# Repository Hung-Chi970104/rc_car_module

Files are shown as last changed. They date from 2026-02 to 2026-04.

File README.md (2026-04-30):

# Rukus: Pocket Robotics Control Computer
Welcome to Rukus! The most powerful and versatile pocket-size robotic control computer that can handle up 18V and 3.2A of peak current. It also features a powerful dual-core RP2040 MCU, allowing users to run heavy computing and even TinyML!

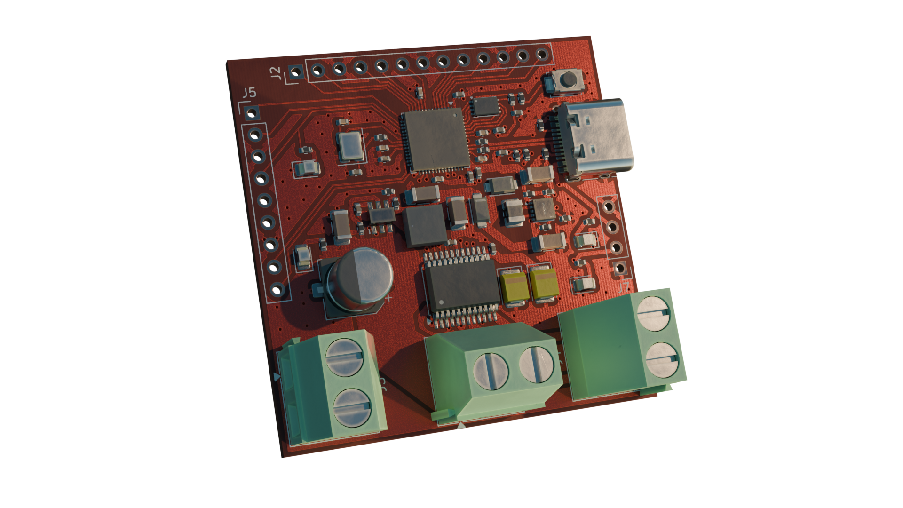
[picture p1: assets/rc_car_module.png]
rendered_image


## Demo Video
https://github.com/user-attachments/assets/a237940f-da78-4733-91b2-979578ba8ca9

https://github.com/user-attachments/assets/f6da3c5c-2f20-4054-9eab-c4b8ad8e2e0a

## Components
- RP2040
- 12MHz Crystal (ABM8-272-T3)
- 4MB Flash Storage (W25Q16JVUXIQ)
- Buck-Boost Switching Regulator 5V to 3V3 (RT6150BGQW)
- Buck-Boost Switching Regulator 12V to 5V (AP64201)
- USB-C (TYPE-C-31-M-12)
- Motor Driver (TB6612FNG)

## PCBs
- 2 layers
- Single-sided component placement
- 2.6mm board thickness
- HASL (with lead) surface finish
- 1oz outer copper weight

### PCB Schematic
schematic

### PCB Layouts
pcb
pcb
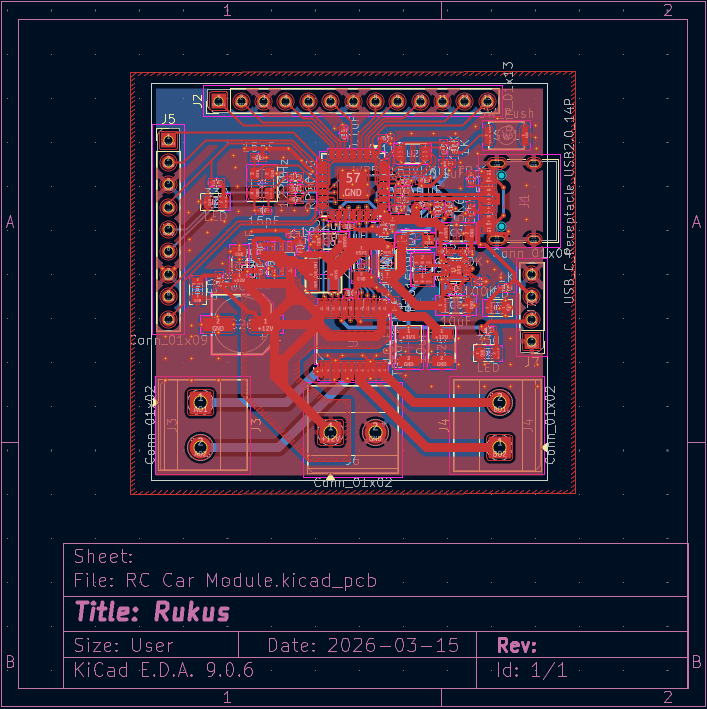
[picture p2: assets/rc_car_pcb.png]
pcb


### 3D Model
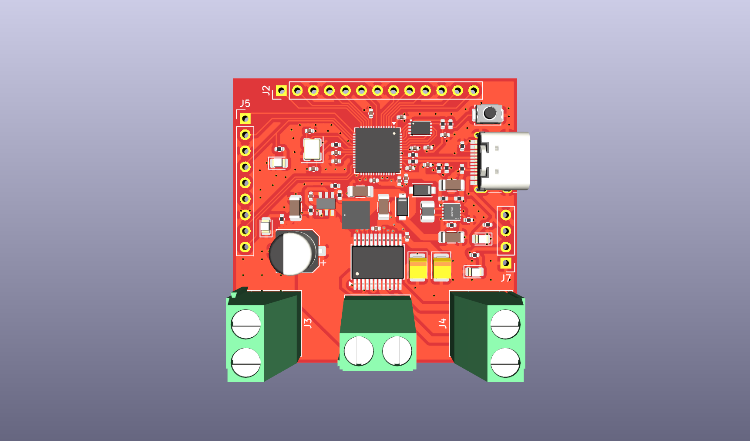
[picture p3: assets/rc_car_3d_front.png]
3d_front

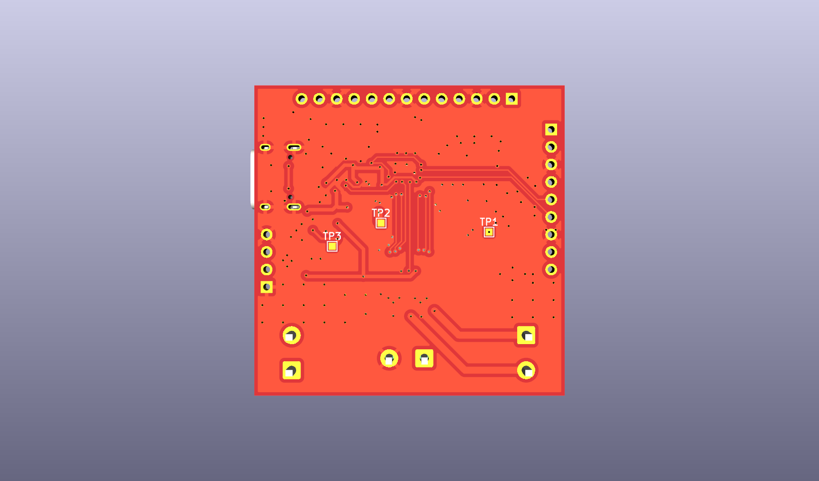
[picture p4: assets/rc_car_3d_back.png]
3d_back


# How to order
- Download the zip file
- Upload the zip file to JLCPCB
- Select PCBA and continue
- Upload BOM.csv and position.csv
- Select the parts and submit payment

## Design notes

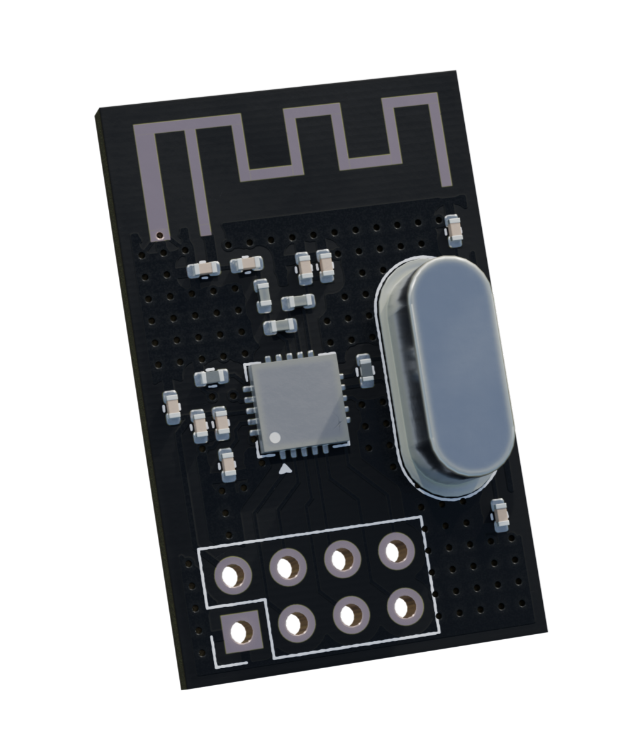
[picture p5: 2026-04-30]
radio/radio.png

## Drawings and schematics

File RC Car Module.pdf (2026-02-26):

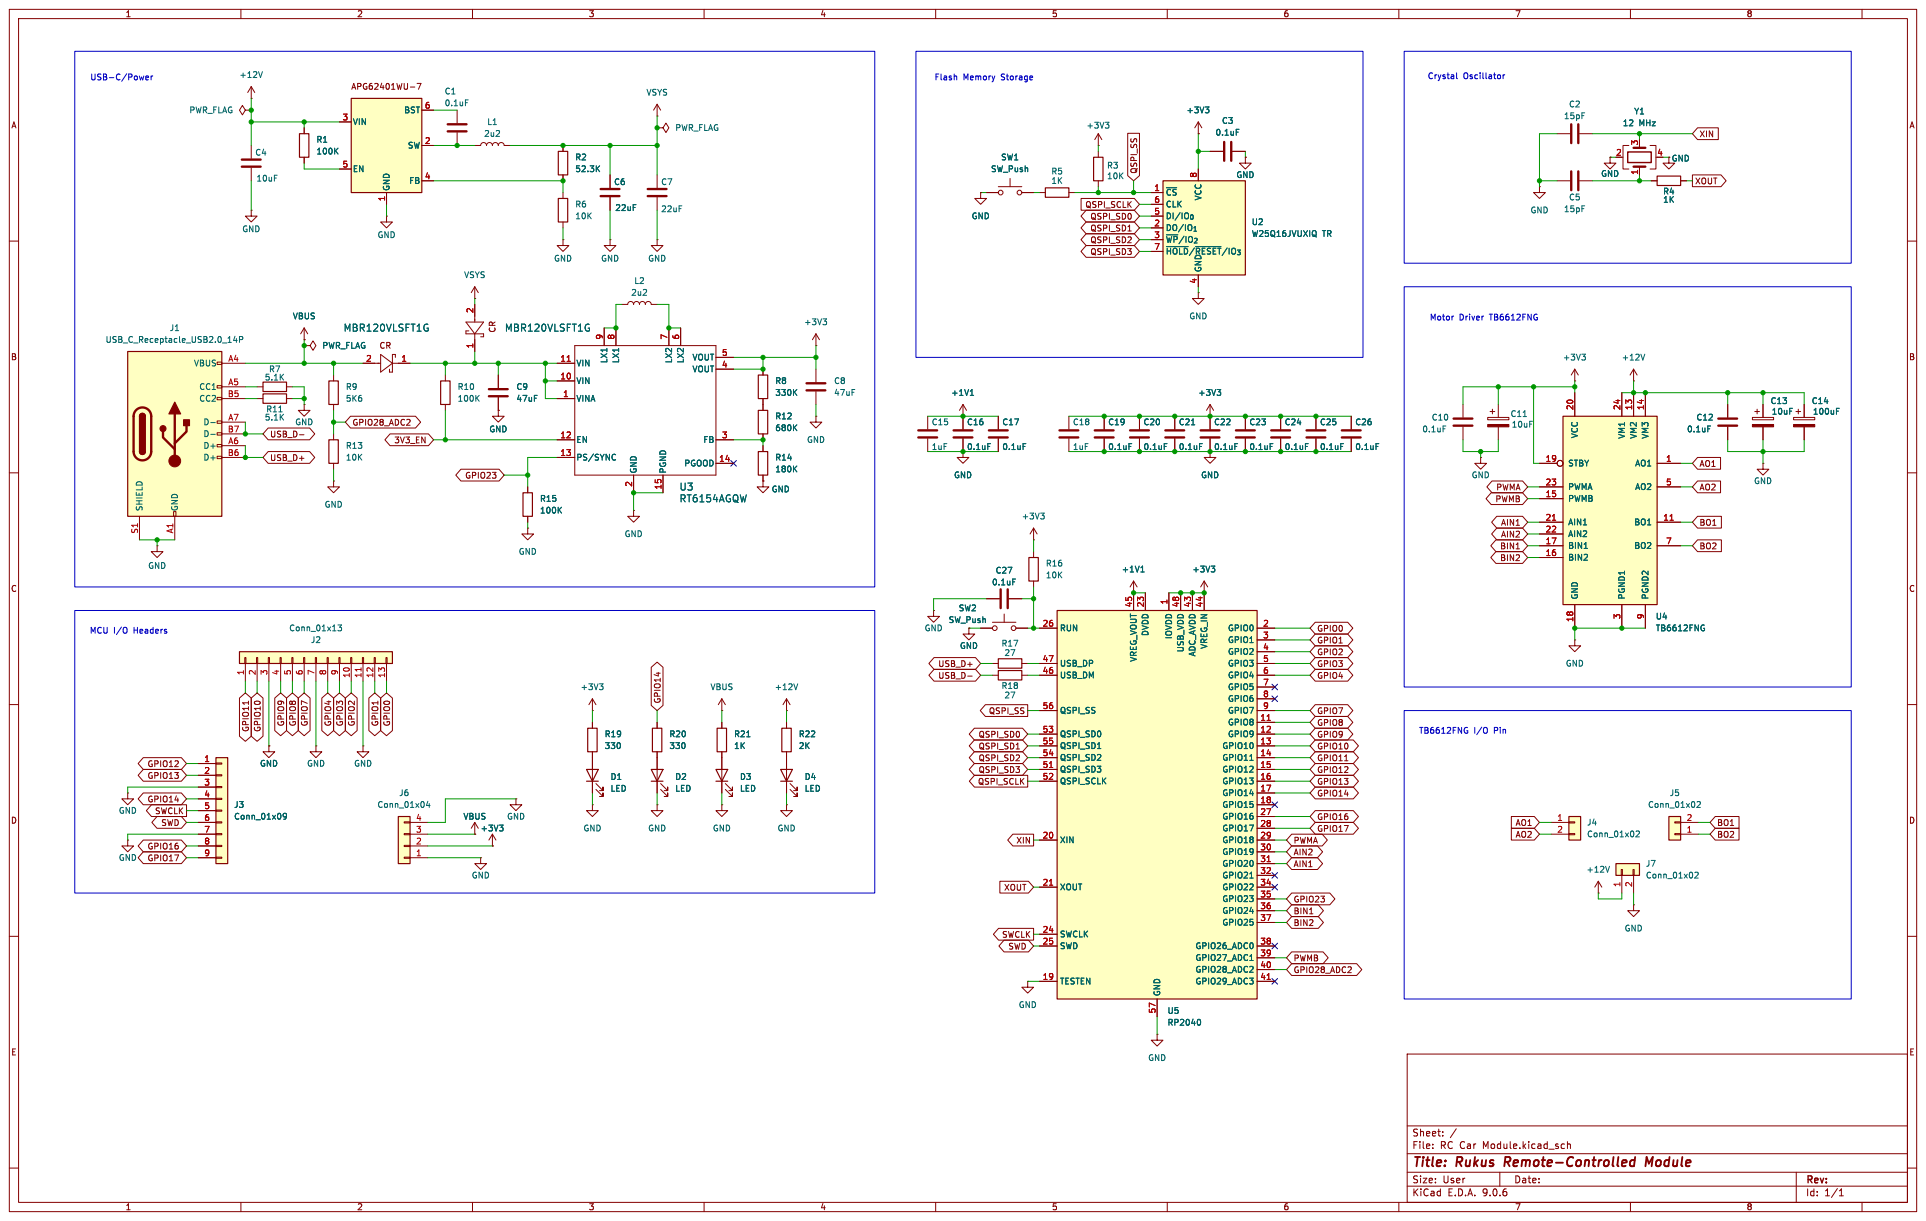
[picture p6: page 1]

1 BST 6 SW 2 FB 4 C1 VSYS

1 BST 6 SW 2 FB 4 GND

6 VOUT 5 VOUT 4 FB 3 PGOOD 14 C9

6 VOUT 5 VOUT 4 FB 3 PGOOD 14 U3 RT6154AGQW

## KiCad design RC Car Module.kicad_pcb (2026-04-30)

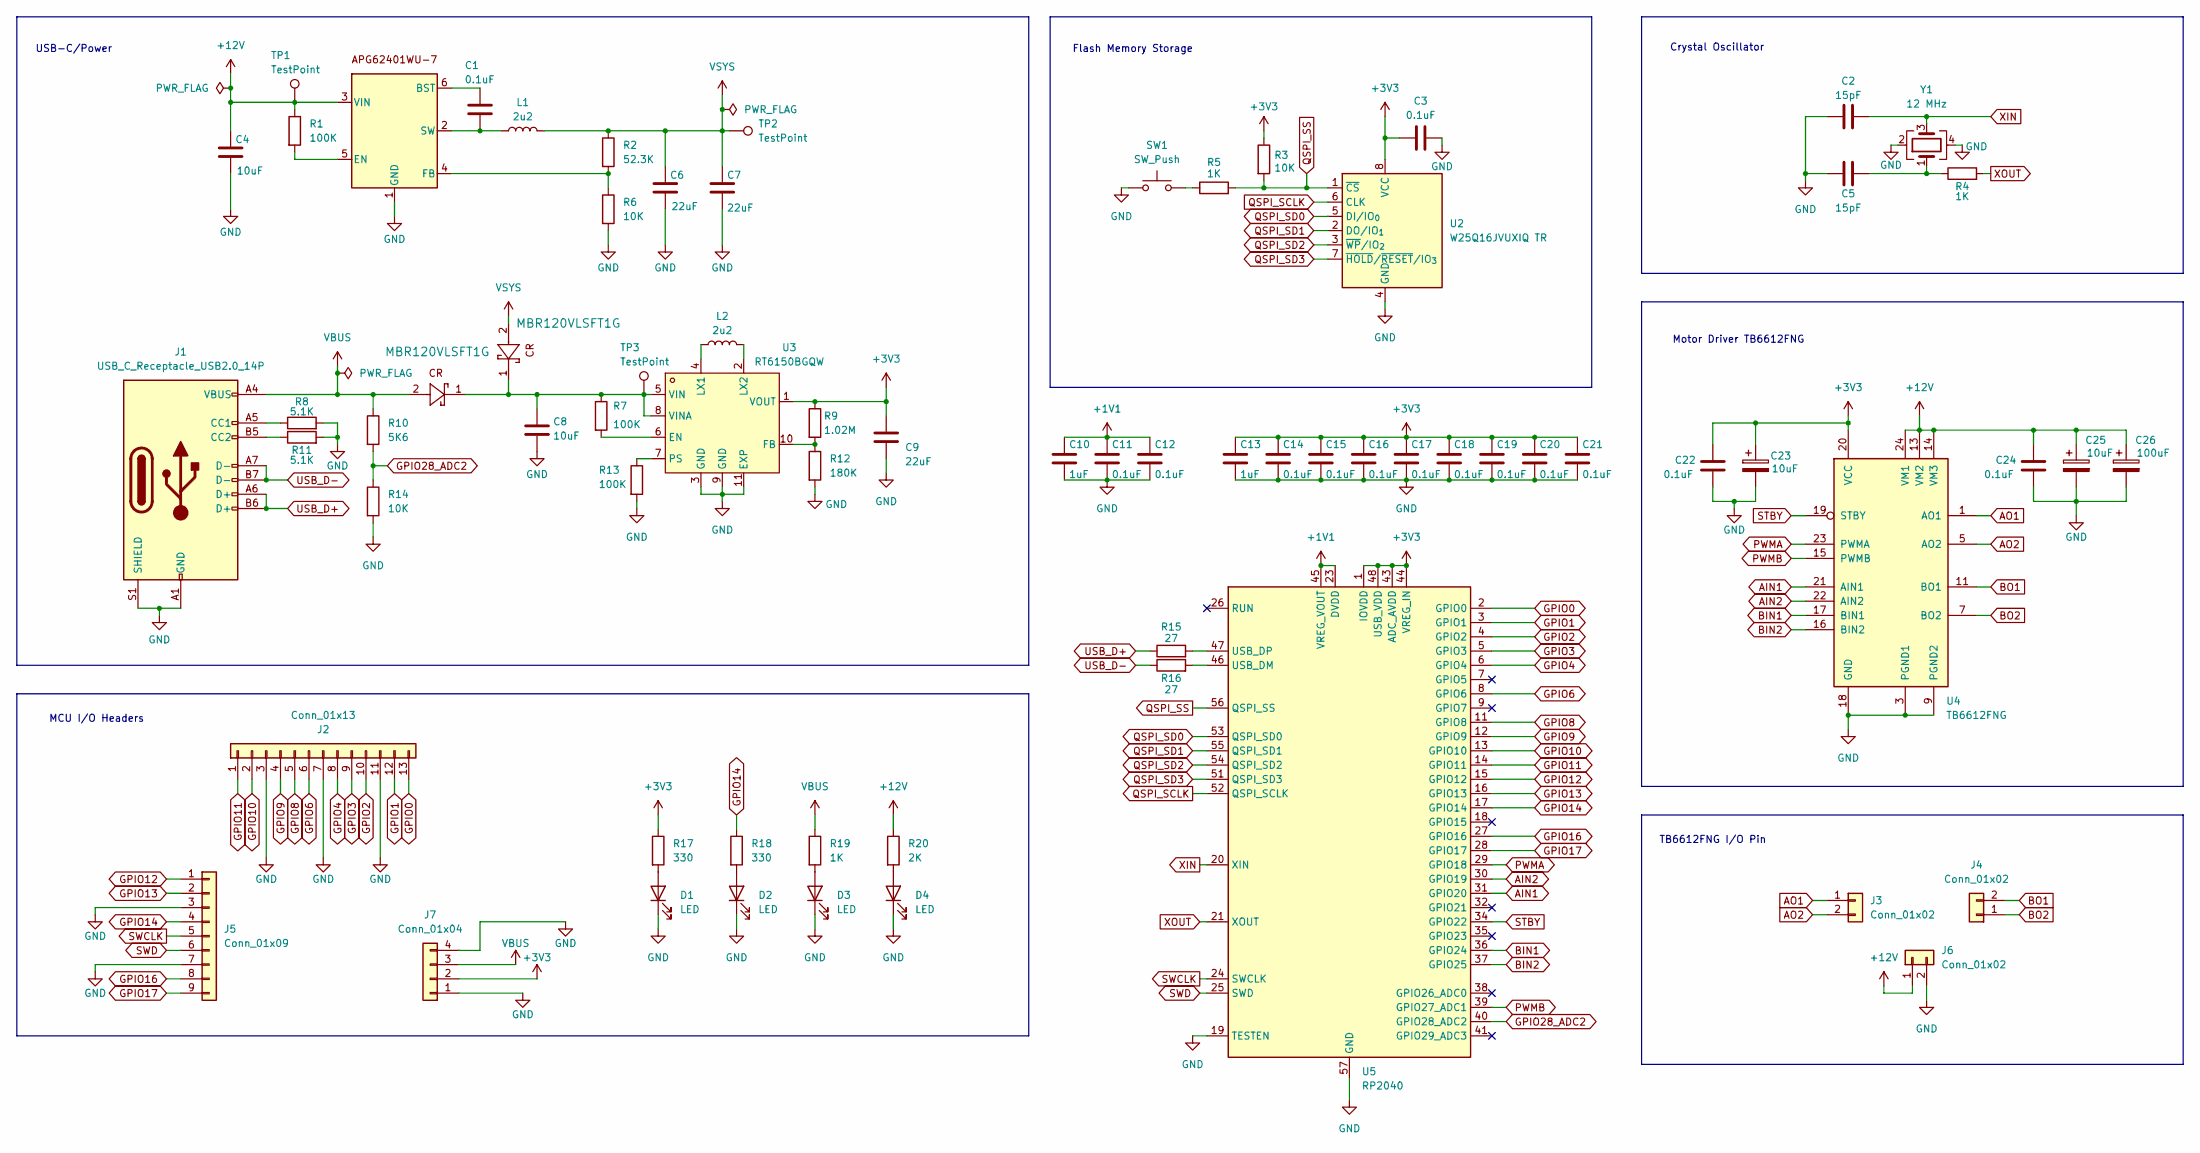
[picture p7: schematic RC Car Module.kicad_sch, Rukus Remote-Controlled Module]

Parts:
1111111111111, 11111111111111: MBR120VLSFT1G; SDO_SOD-123FL_ONS
C1, C3, C11, C12, C14, C15, C16, C17, C18, C19, C20, C21, C22, C24: 0.1uF; C_0402_1005Metric
C2, C5: 15pF; C_0402_1005Metric
C4, C8: 10uF; C_1206_3216Metric
C6, C7, C9: 22uF; C_1206_3216Metric
C10, C13: 1uF; C_0402_1005Metric
C23, C25: 10uF; CP_EIA-3528-15_AVX-H
C26: 100uF; CP_Elec_6.3x7.7
D1, D2, D3, D4: LED; LED_0805_2012Metric
J1: USB_C_Receptacle_USB2.0_14P; USB_C_Receptacle_HRO_TYPE-C-31-M-12
J2: Conn_01x13; PinHeader_1x13_P2.54mm_Vertical
J3, J4, J6: Conn_01x02; TerminalBlock_Phoenix_MKDS-1,5-2-5.08_1x02_P5.08mm_Horizont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
J5: Conn_01x09; PinHeader_1x09_P2.54mm_Vertical
J7: Conn_01x04; PinHeader_1x04_P2.54mm_Vertical
L1: 2u2; IND-SMD_L4.0-W4.0_XAL4030-332MEC
L2: 2u2; L_1008_2520Metric
R1, R7, R13: 100K; R_0402_1005Metric
R2: 52.3K; R_0402_1005Metric
R3, R6, R14: 10K; R_0402_1005Metric
R4, R5, R19: 1K; R_0402_1005Metric
R8, R11: 5.1K; R_0402_1005Metric
R9: 1.02M; R_0402_1005Metric
R10: 5K6; R_0402_1005Metric
R12: 180K; R_0402_1005Metric
R15, R16: 27; R_0402_1005Metric
R17, R18: 330; R_0402_1005Metric
R20: 2K; R_0402_1005Metric
SW1: SW_Push; SW_Push_SPST_NO_Alps_SKRK
TP1, TP2, TP3: TestPoint; TestPoint_Pad_1.0x1.0mm
U1: AP62401WU-7; SOT-23-6
U2: W25Q16JVUXIQ TR; Winbond_USON-8-1EP_3x2mm_P0.5mm_EP0.2x1.6mm
U3: RT6150BGQW; WSON-10_L2.5-W2.5-P0.50-BL-EP; LCSC Part C147972
U4: TB6612FNG; SSOP-24_5.3x8.2mm_P0.65mm
U5: RP2040; QFN-56-1EP_7x7mm_P0.4mm_EP3.2x3.2mm
Y1: 12 MHz; Crystal_SMD_3225-4Pin_3.2x2.5mm

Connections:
+1V1: C10.1, C11.1, C12.1, U5.23 (DVDD), U5.45 (VREG_VOUT), U5.50 (DVDD)
+3V3: C3.1, C9.1, C13.1, C14.1, C15.1, C16.1, C17.1, C18.1, C19.1, C20.1, C21.1, C22.1, C23.1, J7.2, R3.1, R9.1, R17.1, U2.8 (VCC), U3.1 (VOUT), U4.20 (VCC), U5.1 (IOVDD), U5.10 (IOVDD), U5.22 (IOVDD), U5.33 (IOVDD), U5.42 (IOVDD), U5.43 (ADC_AVDD), U5.44 (VREG_IN), U5.48 (USB_VDD), U5.49 (IOVDD)
+12V: C4.1, C24.1, C25.1, C26.1, J6.1, R1.1, R20.1, TP1.1, U1.3 (VIN), U4.13 (VM2), U4.14 (VM3), U4.24 (VM1)
AIN1: U4.21 (AIN1), U5.31 (GPIO20)
AIN2: U4.22 (AIN2), U5.30 (GPIO19)
AO1: J3.1, U4.1 (AO1), U4.2 (AO1)
AO2: J3.2, U4.5 (AO2), U4.6 (AO2)
BIN1: U4.17 (BIN1), U5.36 (GPIO24)
BIN2: U4.16 (BIN2), U5.37 (GPIO25)
BO1: J4.2, U4.11 (BO1), U4.12 (BO1)
BO2: J4.1, U4.7 (BO2), U4.8 (BO2)
GND: C2.1, C3.2, C4.2, C5.1, C6.2, C7.2, C8.2, C9.2, C10.2, C11.2, C12.2, C13.2, C14.2, C15.2, C16.2, C17.2, C18.2, C19.2, C20.2, C21.2, C22.2, C23.2, C24.2, C25.2, C26.2, D1.1 (K), D2.1 (K), D3.1 (K), D4.1 (K), J1.A1 (GND), J1.A12 (GND), J1.B1 (GND), J1.B12 (GND), J1.S1 (SHIELD), J2.3, J2.7, J2.11, J5.3, J5.7, J6.2, J7.1, J7.4, R6.2, R8.2, R11.2, R12.2, R13.2, R14.2, SW1.1, U1.1 (GND), U2.4 (GND), U3.3 (GND), U3.9 (GND), U3.11 (EXP), U4.3 (PGND1), U4.4 (PGND1), U4.9 (PGND2), U4.10 (PGND2), U4.18 (GND), U5.19 (TESTEN), U5.57 (GND), Y1.2, Y1.4
GPIO0: J2.13, U5.2 (GPIO0)
GPIO1: J2.12, U5.3 (GPIO1)
GPIO2: J2.10, U5.4 (GPIO2)
GPIO3: J2.9, U5.5 (GPIO3)
GPIO4: J2.8, U5.6 (GPIO4)
GPIO6: J2.6, U5.8 (GPIO6)
GPIO8: J2.5, U5.11 (GPIO8)
GPIO9: J2.4, U5.12 (GPIO9)
GPIO10: J2.2, U5.13 (GPIO10)
GPIO11: J2.1, U5.14 (GPIO11)
GPIO12: J5.1, U5.15 (GPIO12)
GPIO13: J5.2, U5.16 (GPIO13)
GPIO14: J5.4, R18.1, U5.17 (GPIO14)
GPIO16: J5.8, U5.27 (GPIO16)
GPIO17: J5.9, U5.28 (GPIO17)
GPIO28_ADC2: R10.2, R14.1, U5.40 (GPIO28_ADC2)
unnamed: C5.2, R4.1, Y1.1
unnamed: D1.2 (A), R17.2
unnamed: D2.2 (A), R18.2
unnamed: D3.2 (A), R19.2
unnamed: D4.2 (A), R20.2
unnamed: J1.A5 (CC1), R8.1
unnamed: J1.B5 (CC2), R11.1
unnamed: R5.1, SW1.2
unnamed: C1.1, U1.6 (BST)
unnamed: R1.2, U1.5 (EN)
unnamed: R2.2, R6.1, U1.4 (FB)
unnamed: C1.2, L1.1, U1.2 (SW)
unnamed: R7.2, U3.6 (EN)
unnamed: R9.2, R12.1, U3.10 (FB)
unnamed: L2.1, U3.4 (LX1)
unnamed: L2.2, U3.2 (LX2)
unnamed: R13.1, U3.7 (PS)
unnamed: 1111111111111.1, 11111111111111.1, C8.1, R7.1, TP3.1, U3.5 (VIN), U3.8 (VINA)
unnamed: R16.2, U5.46 (USB_DM)
unnamed: R15.2, U5.47 (USB_DP)
PWMA: U4.23 (PWMA), U5.29 (GPIO18)
PWMB: U4.15 (PWMB), U5.39 (GPIO27_ADC1)
QSPI_SCLK: U2.6 (CLK), U5.52 (QSPI_SCLK)
QSPI_SD0: U2.5 (DI/IO_{0}), U5.53 (QSPI_SD0)
QSPI_SD1: U2.2 (DO/IO_{1}), U5.55 (QSPI_SD1)
QSPI_SD2: U2.3 (~WP/IO_{2}), U5.54 (QSPI_SD2)
QSPI_SD3: U2.7 (~HOLD/~RESET/IO_{3}), U5.51 (QSPI_SD3)
QSPI_SS: R3.2, R5.2, U2.1 (~CS), U5.56 (QSPI_SS)
STBY: U4.19 (STBY), U5.34 (GPIO22)
SWCLK: J5.5, U5.24 (SWCLK)
SWD: J5.6, U5.25 (SWD)
USB_D+: J1.A6 (D+), J1.B6 (D+), R15.1
USB_D-: J1.A7 (D-), J1.B7 (D-), R16.1
VBUS: 1111111111111.2, J1.A4 (VBUS), J1.A9 (VBUS), J1.B4 (VBUS), J1.B9 (VBUS), J7.3, R10.1, R19.1
VSYS: 11111111111111.2, C6.1, C7.1, L1.2, R2.1, TP2.1
XIN: C2.2, U5.20 (XIN), Y1.3
XOUT: R4.2, U5.21 (XOUT)

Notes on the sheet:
USB-C/Power
Flash Memory Storage
Motor Driver TB6612FNG
Crystal Oscillator
TB6612FNG I/O Pin
MCU I/O Headers

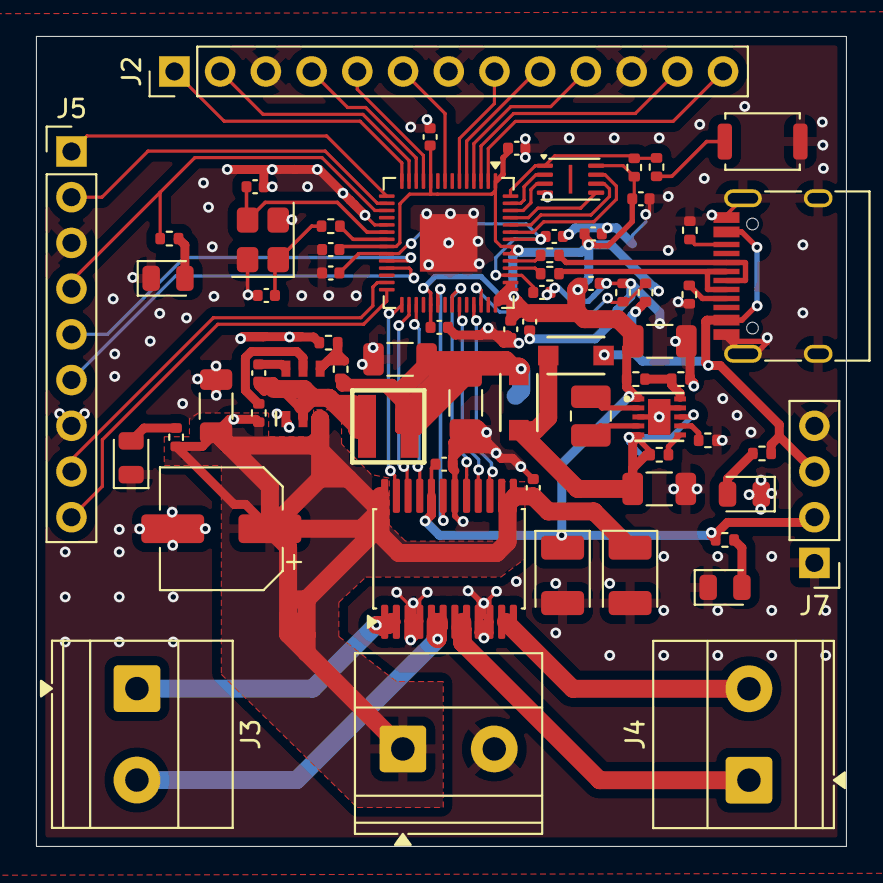
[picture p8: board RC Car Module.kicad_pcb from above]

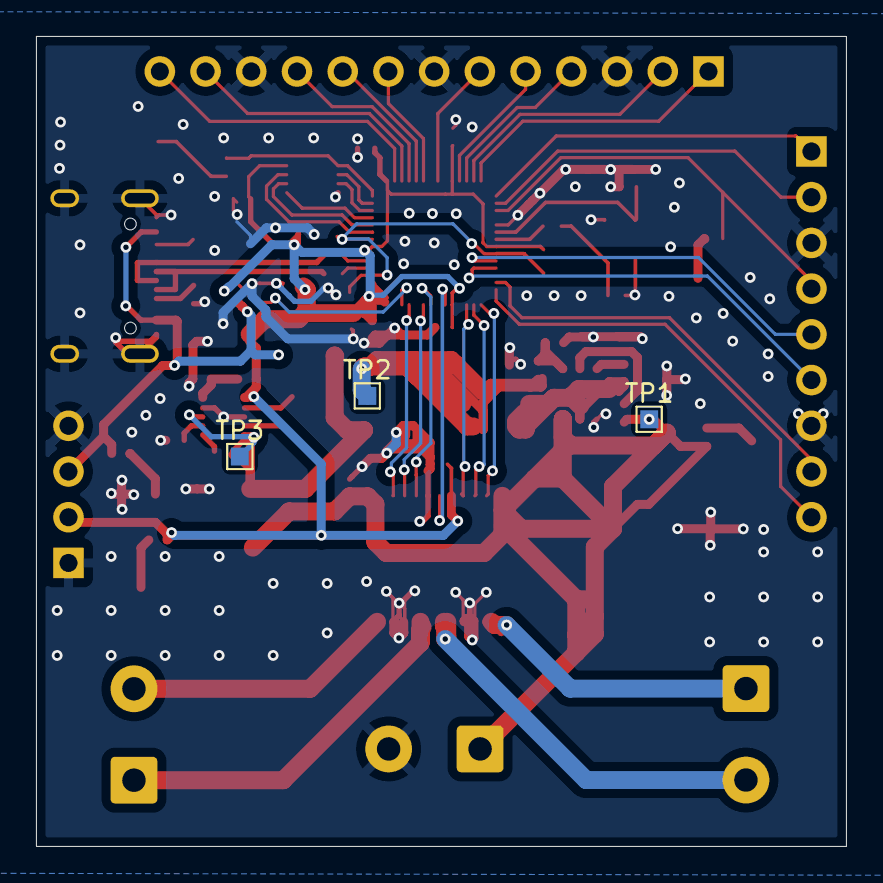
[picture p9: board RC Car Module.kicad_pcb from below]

Board: 2 copper layers, 45.0 x 45.0 mm, 70 parts (3 on the bottom side), 65 nets.

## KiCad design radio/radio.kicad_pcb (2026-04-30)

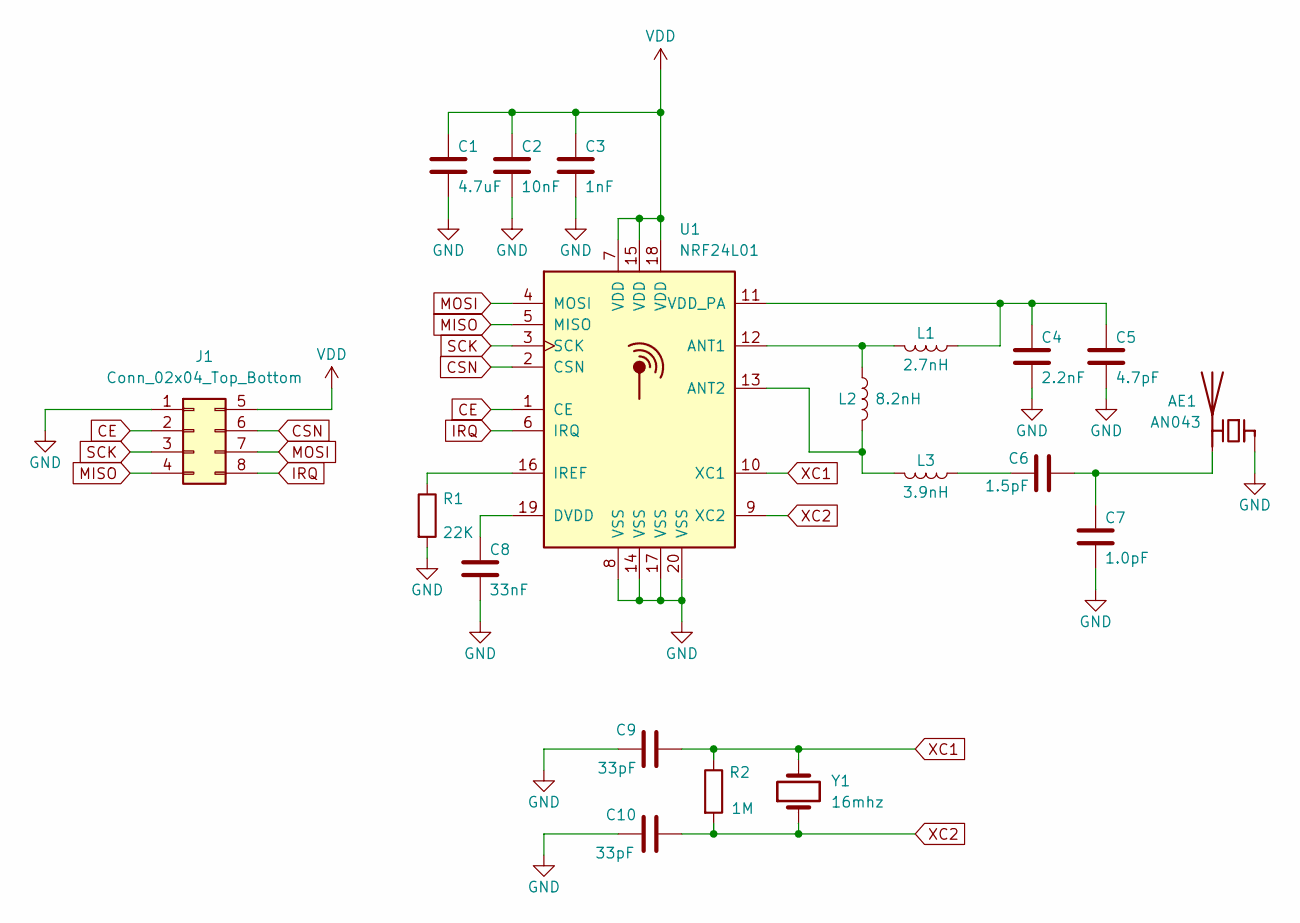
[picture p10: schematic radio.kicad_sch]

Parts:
AE1: AN043
C1: 4.7uF; C_0402_1005Metric
C2: 10nF; C_0402_1005Metric
C3: 1nF; C_0402_1005Metric
C4: 2.2nF; C_0402_1005Metric
C5: 4.7pF; C_0402_1005Metric
C6: 1.5pF; C_0402_1005Metric
C7: 1.0pF; C_0402_1005Metric
C8: 33nF; C_0402_1005Metric
C9, C10: 33pF; C_0402_1005Metric
J1: Conn_02x04_Top_Bottom; PinHeader_2x04_P2.54mm_Vertical
L1: 2.7nH; L_0402_1005Metric
L2: 8.2nH; L_0402_1005Metric
L3: 3.9nH; L_0402_1005Metric
R1: 22K; R_0402_1005Metric
R2: 1M; R_0402_1005Metric
U1: NRF24L01; QFN-20-1EP_4x4mm_P0.5mm_EP2.5x2.5mm
Y1: 16mhz; Crystal_HC49-4H_Vertical

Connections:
CE: J1.2, U1.1 (CE)
CSN: J1.6, U1.2 (CSN)
GND: AE1.1 (FEED), C1.2, C2.2, C3.2, C4.2, C5.2, C7.2, C8.2, C9.1, C10.1, J1.1, R1.2, U1.8 (VSS), U1.14 (VSS), U1.17 (VSS), U1.20 (VSS)
IRQ: J1.8, U1.6 (IRQ)
MISO: J1.4, U1.5 (MISO)
MOSI: J1.7, U1.4 (MOSI)
unnamed: AE1.2 (PCB_Trace), C6.2, C7.1
unnamed: C6.1, L3.1
unnamed: L1.2, L2.1, U1.12 (ANT1)
unnamed: L2.2, L3.2, U1.13 (ANT2)
unnamed: C8.1, U1.19 (DVDD)
unnamed: R1.1, U1.16 (IREF)
unnamed: C4.1, C5.1, L1.1, U1.11 (VDD_PA)
SCK: J1.3, U1.3 (SCK)
VDD: C1.1, C2.1, C3.1, J1.5, U1.7 (VDD), U1.15 (VDD), U1.18 (VDD)
XC1: C9.2, R2.1, U1.10 (XC1), Y1.2
XC2: C10.2, R2.2, U1.9 (XC2), Y1.1

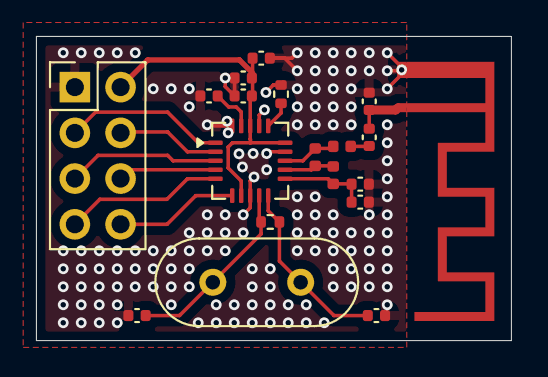
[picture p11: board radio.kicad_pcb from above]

Board: 2 copper layers, 26.4 x 16.9 mm, 19 parts (0 on the bottom side), 17 nets.

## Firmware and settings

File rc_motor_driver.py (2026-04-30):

from machine import Pin
import time #importing time for delay  


# Defining motor pins

#OUT1  and OUT2
In1=Pin(6,Pin.OUT) 
In2=Pin(7,Pin.OUT)  
EN_A=Pin(8,Pin.OUT)



#OUT3  and OUT4
In3=Pin(4,Pin.OUT)  
In4=Pin(3,Pin.OUT)  
EN_B=Pin(2,Pin.OUT)

EN_A.high()
EN_B.high()
# Forward
def move_forward():
    In1.high()
    In2.low()
    In3.high()
    In4.low()
    
# Backward
def move_backward():
    In1.low()
    In2.high()
    In3.low()
    In4.high()
    
#Turn Right
def turn_right():
    In1.low()
    In2.low()
    In3.low()
    In4.high()
    
#Turn Left
def turn_left():
    In1.low()
    In2.high()
    In3.low()
    In4.low()
   
#Stop
def stop():
    In1.low()
    In2.low()
    In3.low()
    In4.low()
    
while True:
    move_backward()

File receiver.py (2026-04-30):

from machine import Pin, SPI
from nrf24l01 import NRF24L01
import time

# 1. Your exact hardware setup
spi = SPI(0, sck=Pin(2), mosi=Pin(3), miso=Pin(4))
csn = Pin(5, mode=Pin.OUT, value=1)
ce = Pin(6, mode=Pin.OUT, value=0)

# 2. Initialize the nRF24L01 module
# The library defaults to channel 46 and a payload size of 16 bytes
nrf = NRF24L01(spi, csn, ce)

# 3. Setup the communication pipe
# Both boards MUST use the exact same 5-byte address to talk to each other
address = b"Node1"
nrf.open_rx_pipe(0, address)
nrf.start_listening()

print("Receiver active! Listening for data...\n")

# 4. Loop and check for incoming messages
while True:
    if nrf.any(): # Check if the RX FIFO has data
        raw_bytes = nrf.recv()
        
        # The library pads short messages with null bytes (\x00), so we strip them
        message = raw_bytes.rstrip(b'\x00').decode('utf-8')
        print(f"Received: {message}")
        
    time.sleep_ms(10) # Tiny delay to keep the RP2040 from running at 100% CPU

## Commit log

2026-02-15 Began adding radio and made a couple changes to the footprints
    [RC Car Module.kicad_pcb, RC Car Module.kicad_sch, radio.kicad_pcb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]
2026-04-30 Update assets
    [RC Car Module.kicad_pcb]
